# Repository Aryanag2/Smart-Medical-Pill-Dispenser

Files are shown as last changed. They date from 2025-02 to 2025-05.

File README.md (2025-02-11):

# Smart Medical Pill Dispenser (SMPD)

## Overview
The **Smart Medical Pill Dispenser (SMPD)** is an automated, cost-effective device designed to help users manage their medications efficiently. The system automatically sorts, stores, and dispenses pills at scheduled times while providing refill alerts and adherence notifications. The project is designed to minimize user dependency on manual sorting and reduce medication errors.

## Features
- **Automated Sorting & Dispensing**: Pills are sorted into dedicated compartments and dispensed at user-defined schedules.
- **Offline Operation**: Requires WiFi only for initial setup and updates; Bluetooth support enables configuration without constant internet access.
- **Refill & Adherence Alerts**: LED indicators and a web app notify users about missed doses and low stock.
- **Battery Backup**: Ensures continued operation during power outages.
- **User-Friendly Interface**: Web-based UI for configuration and monitoring.

## System Components
- **Microcontroller (ESP8266/ESP32)**: Handles scheduling, dispensing, and user notifications.
- **RTC Module**: Maintains accurate time, even during power failures.
- **Stepper Motors & Rotating Disk**: Facilitates pill sorting and controlled dispensing.
- **Weight Sensor (HX711 Load Cell)**: Tracks remaining pill stock and prevents over-dispensing.
- **3D Printed Enclosure**: Built with food-safe PLA/PETG for safe storage and dispensing.

## Repository Structure
```
📂 smart-pill-dispenser
├── 📂 firmware            # Embedded code for microcontroller
├── 📂 web-app             # Web-based UI for user interaction
├── 📂 hardware            # Circuit schematics, PCB designs, and 3D models
├── 📂 docs                # Design documents, proposal, and testing reports
├── 📂 notebooks           # Lab notebooks for individual team members
├── 📜 README.md           # Project overview and setup guide
├── 📜 LICENSE             # Open-source license details
```

## Setup Instructions
### **Hardware Setup**

### **Firmware Installation**

### **Web App Deployment**

## Testing & Validation

## Future Improvements

## License

## Contributors
- **Aditya Perswal** (apersw2)
- **Aryan Gosaliya** (aryanag2)
- **Aryan Moon** (aryanm7)

## Contact

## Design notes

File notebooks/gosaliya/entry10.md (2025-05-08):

### Entry 10: April 20, 2025

**Objectives:**
- Test breadboard setup in machine shop environment  
- Integrate enclosure with buttons and LEDs  
- Prototype 3D-printed trimmer parts to prevent pill jamming  

**Record (Right-Hand Page):**
- Brought breadboard prototype to machine shop for fit check in enclosure  
- Mounted LEDs for dose status and pushbuttons for pairing/refill alerts  
- Observed pill jams in rotating gate design; designed “trimmer” guides to smooth flow  
- Sent trimmer models to SCD for 3D printing in PETG to test clearances  
- Verified button actuation and LED visibility through enclosure cutouts  
- Created logo or ADAPT ( Adi/Aryan Dispenser Advanced Pill Technology) on CANVA

**Figures (Left-Hand Page):**
- `wooden-enclosure-with-logo-leds.png` — Photo of breadboard inside enclosure with buttons and LEDs installed and 3d printed trimmers installed  
- `logo.png` — logo for ADAPT

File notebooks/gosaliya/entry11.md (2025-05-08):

### Entry 11: April 27, 2025

**Objectives:**
- Validate full PCB functionality  
- Develop Electron desktop app for device control  
- Finalize firmware: HX711 calibration, BLE button link, flash-based schedule storage, and UI polish  

**Record (Right-Hand Page):**
- Received and tested revised PCB; all subsystems powered, no overheating  
- Calibrated HX711 in firmware for ±0.1 g accuracy; updated `readWeight()` routine  
- Mapped BLE “pair” button to trigger dispense and status commands  
- Implemented SPIFFS-based schedule storage in flash memory; supports up to 10 dose-times  
- Built Electron app with React UI: “Dispense Now,” “View Schedule,” and real-time status indicators  
- Iterated UI for user-friendly labels, feedback spinners, and error dialogs  

**Figures (Left-Hand Page):**
- `final-electron-demo.png` — Screenshot of Electron app dashboard  
- `working-pcb.png` — Photo of working PCB with LEDs and button mounted

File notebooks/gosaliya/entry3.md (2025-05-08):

### Entry 3: February 15, 2025

**Objectives:**
- Finalize mechanical enclosure design for machine shop  
- Design power-jack & backup battery circuit  
- Prototype enclosure & power circuit in KiCAD  

**Record (Right-Hand Page):**
- **KiCAD draft:**  
  - Created enclosure power-circuit schematic with DC jack, regulator footprints, and battery connector  
  - Labeled silkscreen for mounting holes and connector orientation  
  - Noted need for 12 V Li-ion rechargeable pack (≈2200 mAh)  
- **Battery backup:**  
  - Drew schematic for seamless switchover (diode-OR) between wall adapter and Li-ion pack  
  - Sized polyfuse and decoupling caps for 1 A peak load  
- **Component decision:**  
  - Switched from ATmega328 + HC-05 to ESP32-WROOM for built-in BLE, extra GPIO, and simplified PCB routing. No need for external RTC module

**Figures (Left-Hand Page):**
- `power.png` – power-circuit schematic  
- `battery_2way.png` – Battery-backup

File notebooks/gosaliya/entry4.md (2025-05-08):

### Entry 4: February 25, 2025

**Objectives:**
- Demonstrate breadboard prototype of interface, power, and mechanical subsystems  
- Validate core module integrations  
- Assess feasibility of rotating funnel design  

**Record (Right-Hand Page):**
- **Breadboard setup:**  
  - Used ESP32 dev kit (with onboard USB) for MCU and programming  
  - Connected DS3231 RTC module, HX711 + 1 kg load cell, standard servo, LEDs, and pushbutton  
- **Firmware validation:**  
  - Moved servo to 0 °, 90 °, and 180 ° positions reliably  
  - Verified load-cell reading lights LED when weight threshold exceeded  
  - Tested Bluetooth pairing via button and simple LED on/off commands  
- **Design evaluation:**  
  - Consulted machine shop: rotating funnel + stepper had clearance and alignment issues  
  - Decided to switch to a servo-driven shutter for dispensing  
- **Next steps:**    
  2. work with machine shop and breadboard-test the  design  
  3. Refine firmware timing and calibration for the new mechanism  

**Figures (Left-Hand Page):**
- `breadboard.png` — Photo of the breadboard prototype setup

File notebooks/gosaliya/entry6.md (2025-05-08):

### Entry 6: March 10, 2025

**Objectives:**
- Final team meeting before full breadboard demo  
- Refactor and modularize firmware functions  
- Calibrate sensors in code & verify accuracy  
- Note: web app functionality pending — focus remains on breadboard firmware  

**Record (Right-Hand Page):**
- **Modular code:**  
  - Split sketch into `dispensePill()`, `indexCompartment()`, `readWeight()`, `handleBTCommands()`  
- **Sensor calibration:**  
  - Tested with 1 g, 2 g, and 5 g weights; adjusted calibration factor for consistent ±0.2 g readings  
- **Persistence & scheduling stub:**  
  - Prepared SPIFFS routines using `Preferences` to store dose-times offline  
  - Added RTC-driven trigger logic; UI hookup deferred until web-app code is ready  
- **Failsafe & debugging:**  
  - Added error-LED blink on stall detection  
  - Serial logging timestamps each state and error for tuning timing constants
- Received mechanical enclosure from machine shop

**Figures (Left-Hand Page):**
- `basic-sketch.png`- Basic sketch showing servo control
- `wooden-enclosure.png` - Received mechanical enclosure from machine shop with servos, laod cell and pills

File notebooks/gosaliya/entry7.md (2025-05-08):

### Entry 7: March 17, 2025

**Objectives:**
- Conduct full breadboard integration demo  
- Validate end-to-end dispensing cycle  
- Identify firmware refinements before design review  

**Record (Right-Hand Page):**
- Assembled ESP32, , load-cell amplifier, servo motors, LEDs, button, and battery backup on the breadboard  
- Uploaded consolidated firmware with modular functions (`dispensePill()`, `indexCompartment()`, `readWeight()`, `handleBTCommands()`)  
- Ran demo sequence: wake, dispense dose, verify weight, signal success via LED  
- Measured average dispense latency: 1.8 s  
- Logged dispense errors for tuning threshold and timing constants  
- Team feedback: shutter mechanism consistent; LED alerts clear; adjust weight threshold by ±0.3 g  
- Prepared notes for upcoming design review and final paper  

**Figures (Left-Hand Page):**
- `breadboard.png` – Photo of integrated breadboard assembly  
- `basic-blueooth.png` - Basic bluetooth connectivity from ES32

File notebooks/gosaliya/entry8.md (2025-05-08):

### Entry 8: April 6, 2025

**Objectives:**
- Prototype web interface for device control & monitoring  
- Integrate JavaScript frontend with device via BLE/WebSocket  
- Test UI commands for dispensing and status updates  

**Record (Right-Hand Page):**
- Created basic web app structure in `index.html` with buttons for “Dispense Dose” and “Check Status”  
- Implemented BLE connection and command handlers in `main.js`  
- Developed `demo.js` to wire up UI buttons to BLE commands and display device responses  
- Verified browser↔device communication: “Dispense” and “Status” operations complete in 2–3 s  
- Noted occasional packet loss under weak signal; plan to add retry logic and visual feedback (spinner)  
- Defined next steps: full feature integration, robust error handling, and UI styling  

**Figures (Left-Hand Page):**
- `basic-webapp.png` — Screenshot of web app dashboard with control buttons

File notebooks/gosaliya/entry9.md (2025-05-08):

### Entry 9: April 13, 2025

**Objectives:**
- Test first full PCB revision (PCB1) with all subsystems  
- Diagnose power-subsystem failures (trace width, overheating)  
- Perform tolerance & thermal analysis  
- Design and order revised power-only PCB  

**Record (Right-Hand Page):**
- PCB1 arrived; soldered ESP32, hx711, servos, LEDs & button, and power regulators  
- Powered on: observed 5 V rail drop to 4.2 V under 500 mA load and regulator surface overheating after ~5 min  
- Measured PCB trace resistance; calculated I²R losses vs. expected voltage drop  
- Conducted tolerance analysis on regulator dropout voltage and copper trace ampacity  
- Determined that power traces (0.3 mm width) are undersized for peak currents  
- Decided to isolate power stage onto its own PCB with 1 mm-wide traces, added thermal vias and larger copper pours  
- Placed order for power-only PCB revision; delivery expected in 2 weeks  

**Figures (Left-Hand Page):**
- `final-pcb.png` - Kicad for PCB ordered

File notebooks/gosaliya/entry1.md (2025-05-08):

### Entry 1: January 25, 2025

**Objectives:**
- Summarize challenges in medication adherence for seniors  
- Review existing smart-dispensing solutions on the market  
- Define clear design goals (cost, accuracy, connectivity, power backup)  
- Sketch the initial system concept and high-level architecture  

**Record (Right-Hand Page):**
- **Demographics & adherence:**  
  - U.S. 65+ population grew by 9.4 % from 2020 to 2023  
  - 54 % of seniors take four or more prescription drugs  
  - 50 % of doses are forgotten or mistimed  
- **Financial impact:**  
  - Average annual medication spend ≈ \$800 per user  
  - Non-adherence wastes up to 50 % of that cost annually  
- **Competitive analysis:**  
  - **Hero dispenser:** \$540/year subscription; Wi-Fi only  
  - **MedMinder & Petal:** similar price points, require constant internet  
- **Identified user needs:**  
  - **Upfront cost ≤ \$250**; **server fees ≤ \$5/month**  
  - **Offline-first operation** after initial Bluetooth setup  
  - **Simple interface:** LEDs for dose & refill status; mobile web-app alerts  
  - **Battery backup** to cover power outages and maintain RTC  
- **Design targets:**  
  - **Dispensing accuracy ≥ 98.4 %** per scheduled dose  
  - **Alert latency < 5 seconds** from scheduled dispense time  
  - **Refill notification** when pill stock ≤ 10 %  
- **Next steps:**  
  1. Finalize and print high-level block diagram  
  2. Source candidate modules for each subsystem  
  3. Prepare parts list for initial breadboard prototyping  

**Figures:**
- `hero_device.jpeg` – Photo of the Hero smart dispenser (competitor device)  
- `hero_blockdiagram.png` – Hero’s high-level system block diagram

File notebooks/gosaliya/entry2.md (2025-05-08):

### Entry 2: February 8, 2025

**Objectives:**
- Decompose system into major subsystems  
- Survey existing modules & designs  
- Finalize top-level parts list  

**Record (Right-Hand Page):**
- **Six subsystems identified:**  
  1. Real-Time Clock + battery backup  
  2. MCU & comms (ESP8266 → ESP32)  
  3. Motor control (stepper & servo drivers)  
  4. Weight sensing (HX711 + load cell)  
  5. Mechanical housing & pill routing  
  6. User interface (LEDs, buzzer, button, web-app)  
- **Module survey notes:**  
  - RTC: DS3231 (±2 ppm accuracy, coin-cell backup)  
  - MCU: ESP8266 dev-kit prototyping → ESP32-WROOM for more I/O & BLE  
  - Drivers: L298N for stepper; HS-318 servo for funnel shutter  
  - Sensor: 1 kg load cell + HX711 amplifier (±0.2 g)  
  - Enclosure: PLA 3D-print core, wood frame from machine shop  
- **Integration sketch:**  
  - Data-flow arrows between MCU, sensors, actuators, and UI drawn for clarity  
- **Final parts list:**  
  - ESP32-WROOM-32D  
  - DS3231 RTC module  
  - HX711 + 1 kg load cell  
  - L298N motor driver board  
  - HS-318 servos × 2  
  - LEDs: power, mode, refill, and 3× compartment indicators  
  - Pushbutton (pairing/reset)  
  - Regulators: 12 V→5 V (LM7805), 5 V→3.3 V (LP2950)  
  - 12 V Li-ion backup pack  

**Figures (Left-Hand Page):**
- `esp32.jpeg` – ESP32-WROOM-32D module photo  
- `ds3231.jpeg` – DS3231 RTC module photo

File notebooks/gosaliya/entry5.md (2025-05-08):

### Entry 5: March 3, 2025

**Objectives:**
- Kick off firmware development on the breadboard  
- Validate control of mechanical & sensing subsystems  
- Lay groundwork for mobile/web interface commands  

**Record (Right-Hand Page):**
- **Arduino IDE setup:**  
  - Installed ESP32 core, HX711 and Servo libraries  
  - Created sketch with `setup()` and `loop()` stubs  
- **Breadboard firmware tests:**  
  - Servo on pin 4 moved to 0°, 90°, and 180° reliably  
  - Stepper via L298N indexed compartments; tuned `stepDelay` to correct step errors  
  - Load cell calibrated using `scale.set_scale()` and `scale.tare()`, LED on pin 12 lights when weight threshold exceeded  
- **Bluetooth pairing & UI stub:**  
  - Button on pin 5 initiates pairing mode via BLE  
  - Sketch logs “LED ON”/“LED OFF” commands over Serial; full web-app integration to come  
- **Code structure:**  
  - Implemented basic state machine (`IDLE`, `PAIRING`, `DISPENSE`, `ERROR`) for early prototyping  

**Figures (Left-Hand Page):**
- `code_flow.png` – Firmware Code Flow Diagram  
- `data_flow.png` – Data Flow Diagram

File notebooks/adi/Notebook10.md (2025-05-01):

# Notebook 10

**Date:** April 20th, 2025

## Objectives
1. Power the Breadboard with the Power Only PCB
2. Create a Last Chance PCB with through holes only
3. Switch to programming with a breakout board
4. Implement 3D prints for compartment trimmers

## Record of Work

Created the "Last Chance" PCB and ordered it. Hopefully it comes in on time, this is our 6th and final PCB order likely. Used through holes only so when it does come we can solder it very quickly.

Need to buy solder paste still for the ESP32-WROOM-32D. I don't remember if I wrote in why we switched to 32D from 32U but it was because it had an antenna and only costed a few more cents.

### Last Chance Schematic View
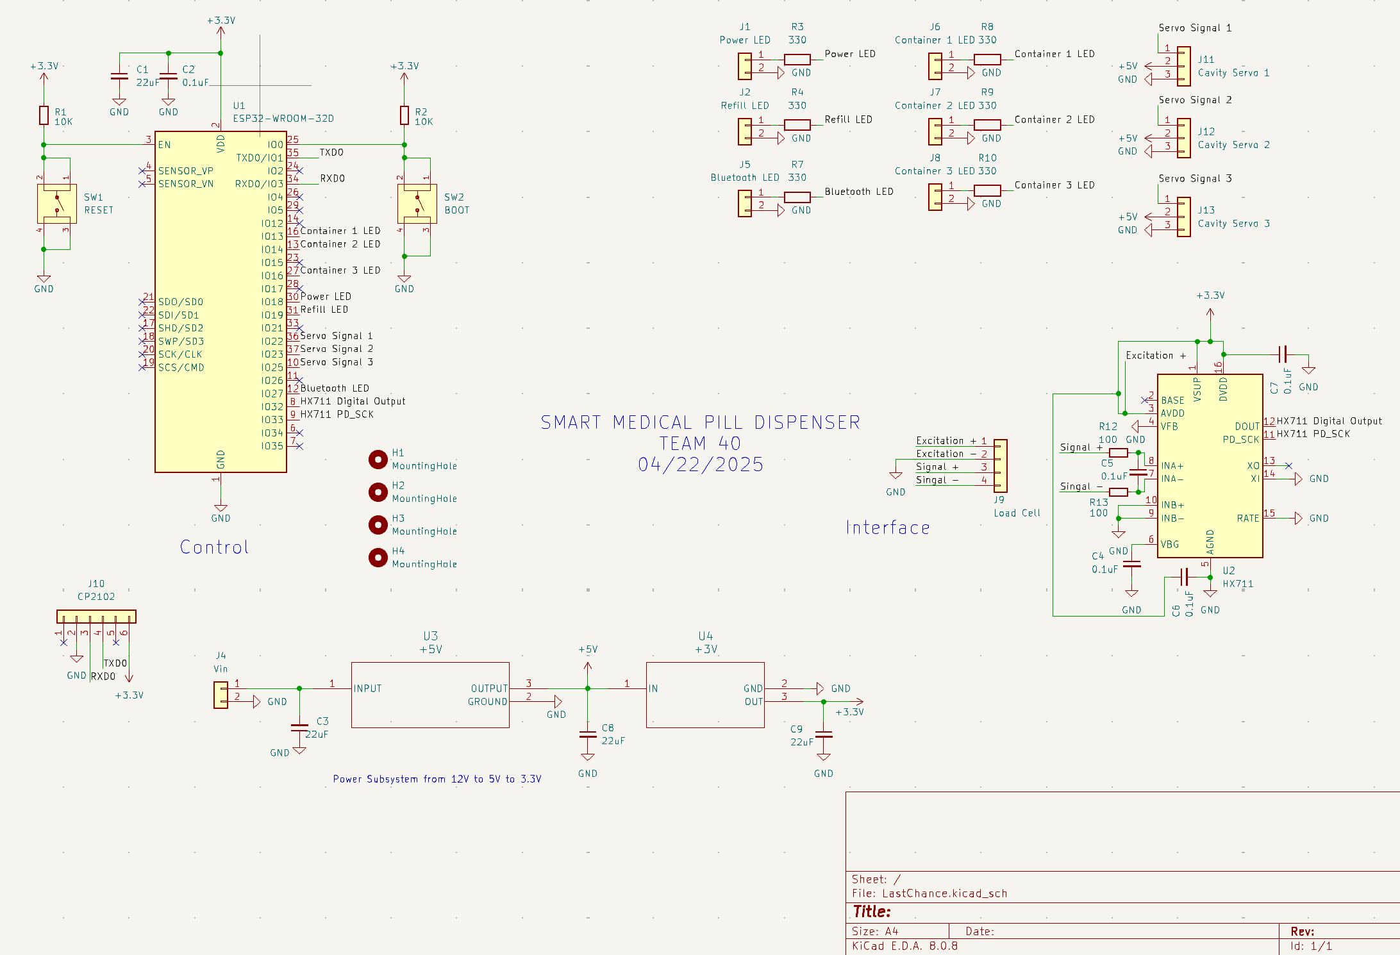
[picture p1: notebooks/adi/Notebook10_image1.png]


### Last Chance PCB View
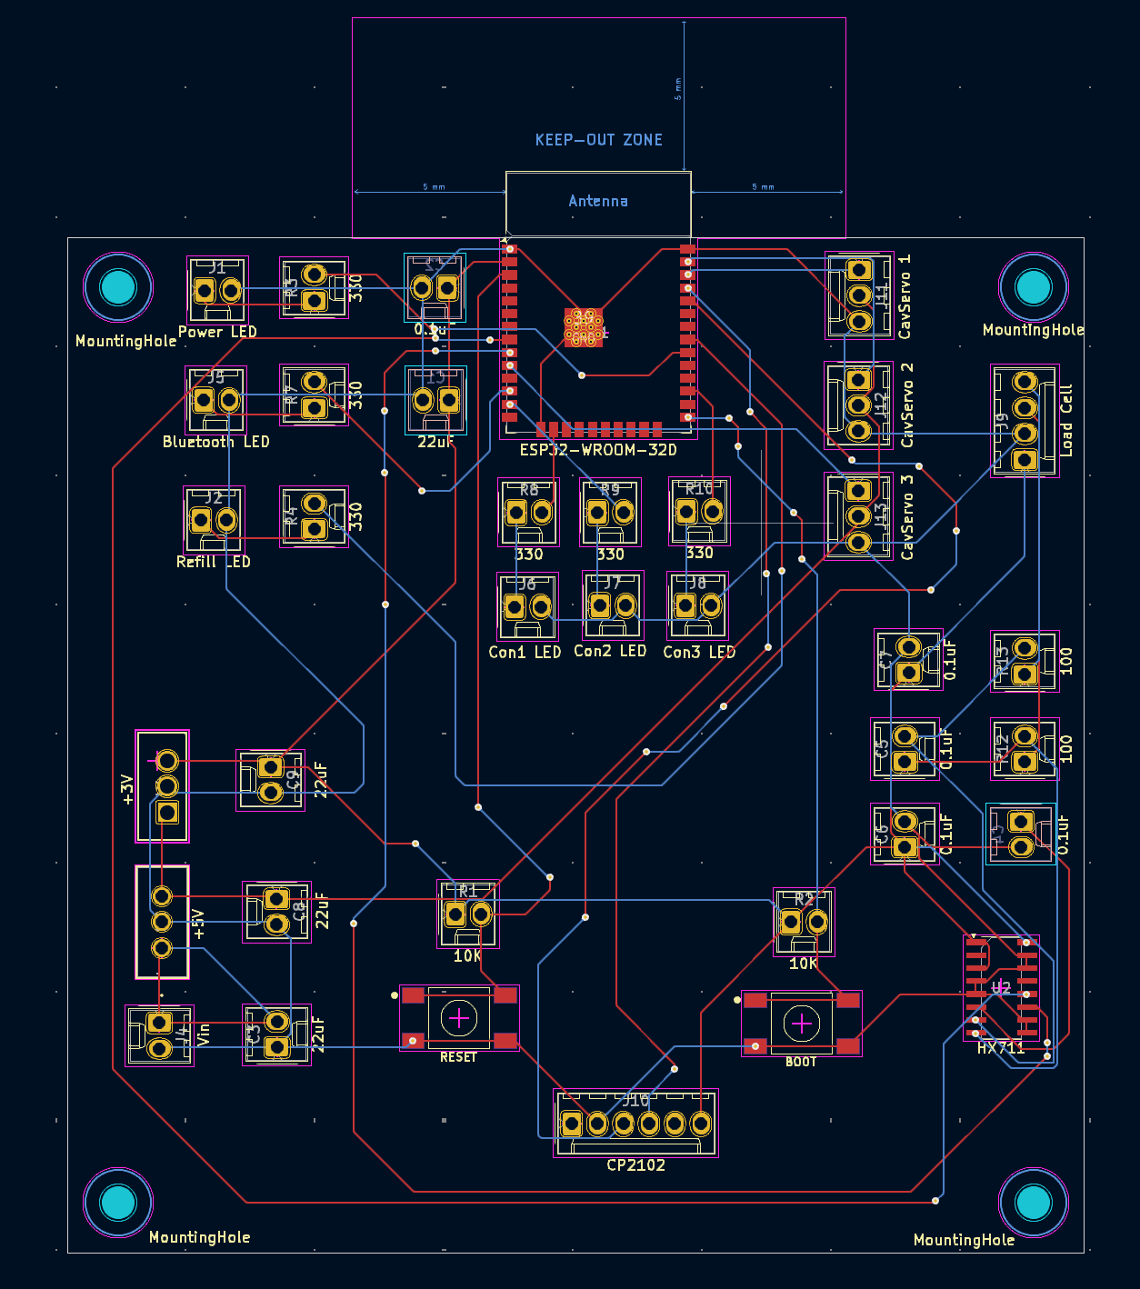
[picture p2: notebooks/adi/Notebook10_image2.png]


The arduino code is having some issues with dispensing on time when the scheduled medications pop up. The microcontroller can take commands pretty quickly but it does them one at a time. Maybe it is having issues because we are sending so many commands at once. Right now we have about 1,400 lines of code in our Arduino IDE, I think I can drop that to 900 though and clean up / refactor the code a ton.

### Arduino Code
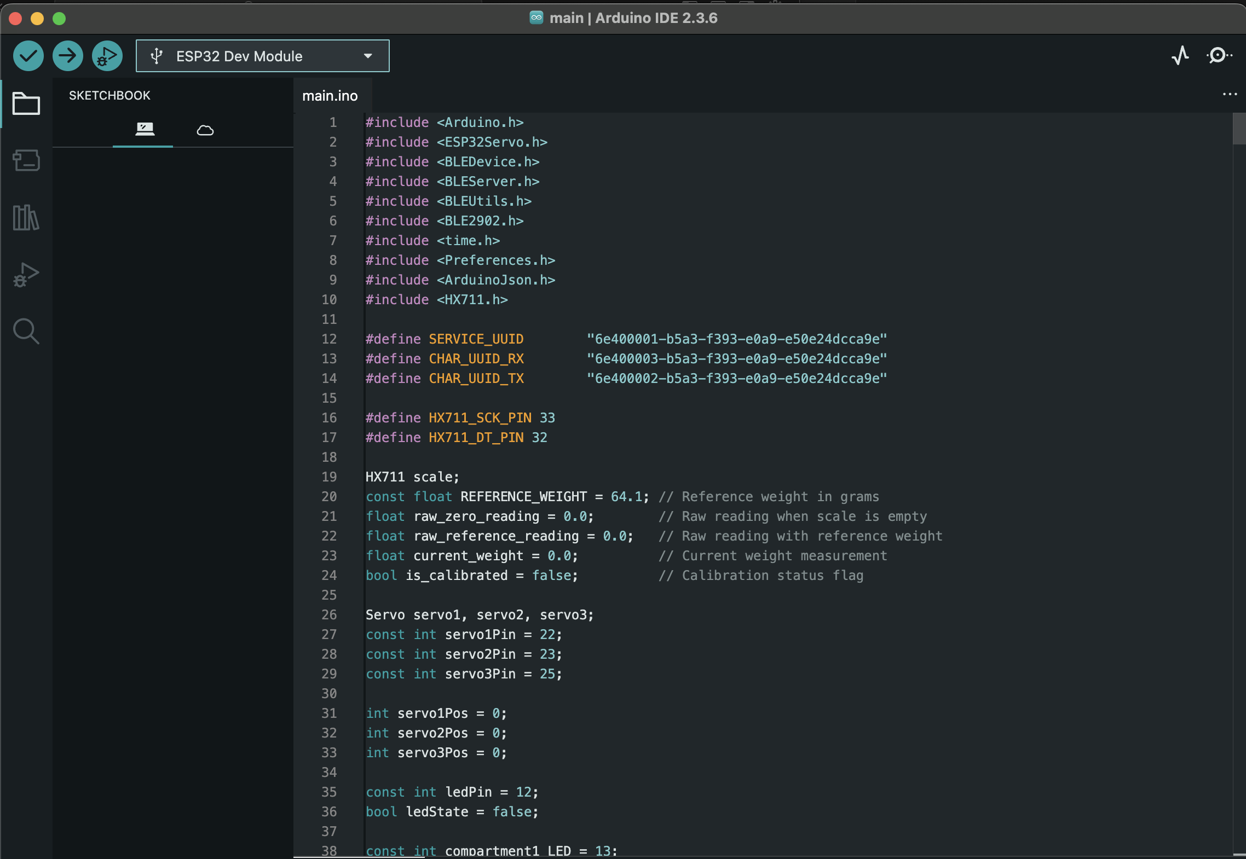
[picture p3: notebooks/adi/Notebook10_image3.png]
Arduino Code


The USB-UART breakout board should help a ton. We broke so many Micro USB ports because of poor soldering or didn't have the FT232RL soldered properly.

### CP2102 Breakout Board
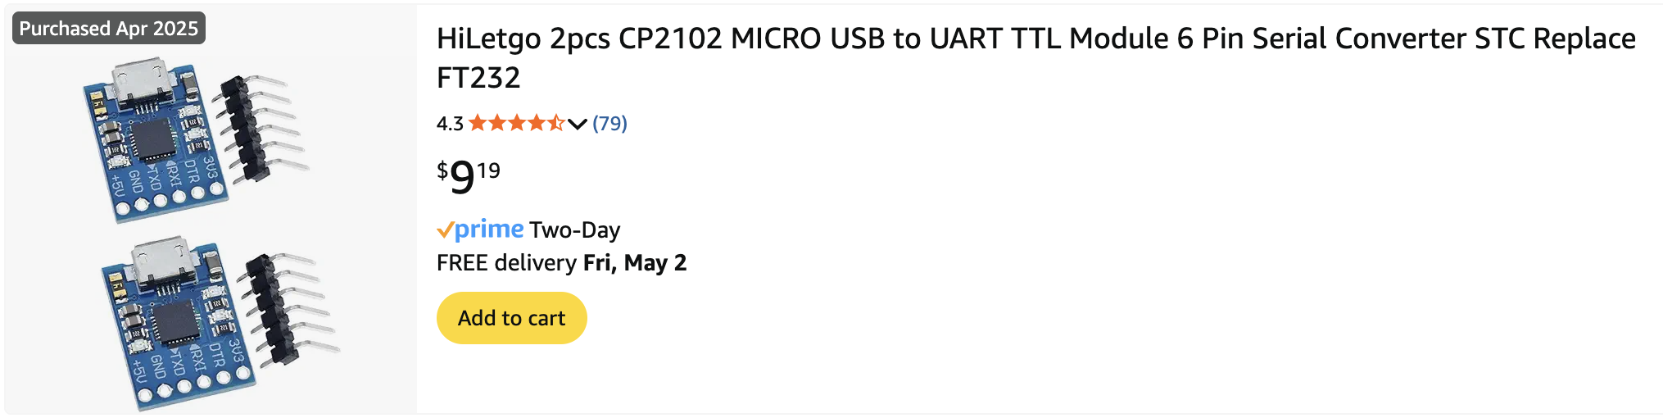
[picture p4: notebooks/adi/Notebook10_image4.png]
CP2102 Breakout Board


Learned AutoCAD for this class. This trimmers should come in soon, will go to SCD and have them printed out. They said it should only cost about $1.80.

### 3D Prints
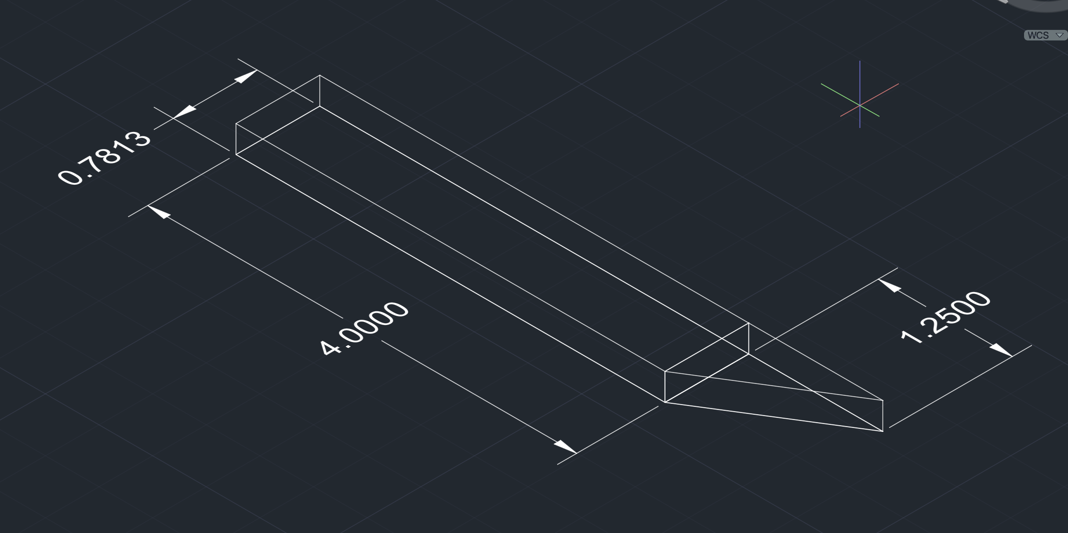
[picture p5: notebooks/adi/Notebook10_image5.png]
Compartment 1

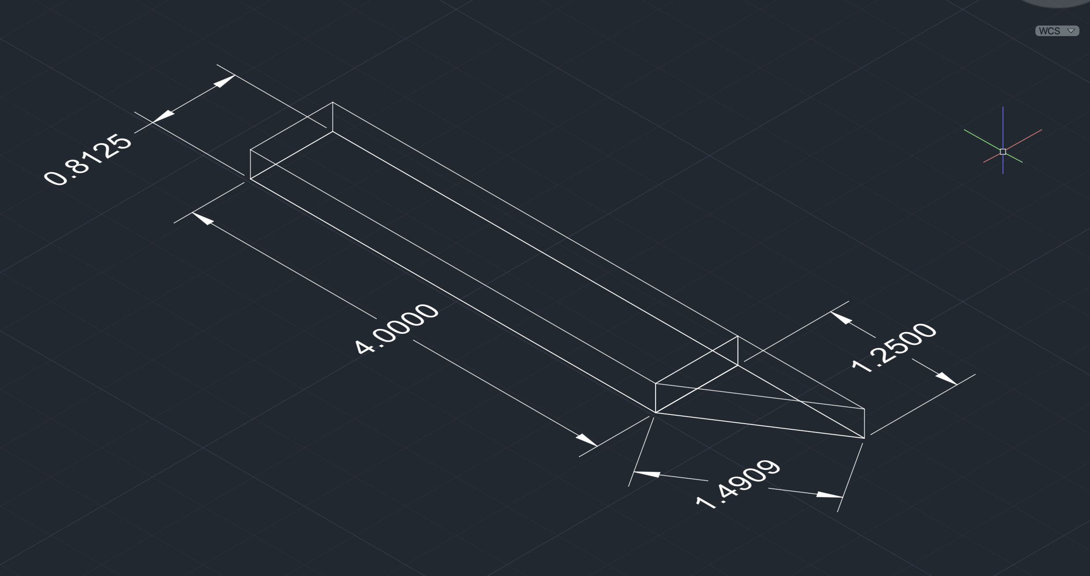
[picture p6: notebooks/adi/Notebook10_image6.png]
Compartment 2

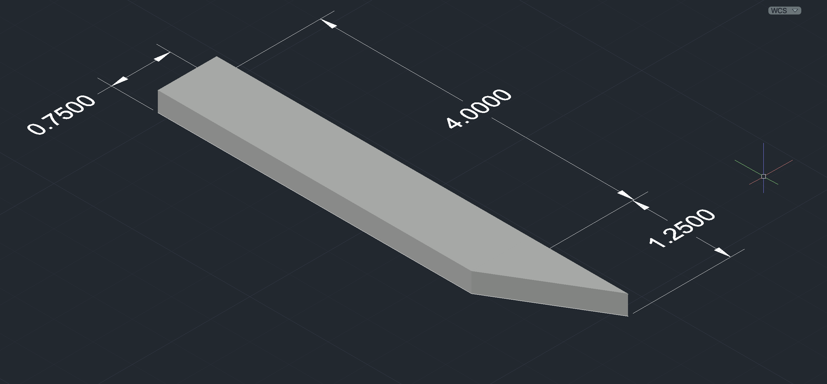
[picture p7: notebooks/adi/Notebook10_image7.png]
Compartment 3


## Personal Thoughts
The power only PCB is working correctly outputting around 5.07V and 3.301V respectively. Tried to put power in directly to the output pins of the regulator through holes of the original PCB but that ended up leading to 1.7V for the 5V through hole or 0.6V for the 3.3V through hole. Going to need to figure out a way to power the final design with this PCB. That seems to be having the power subsystem on the PCB and the rest outside it. Hopefully we get a good set of points from the final demo rubric, and the final last chance PCB can come in time.

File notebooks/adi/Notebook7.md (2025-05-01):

# Notebook 7

**Date:** March 29th, 2025

## Objectives
1. Complete PCB for CP2102 for Order 3
2. Complete PCB for FT232RL for Order 4
3. Order Extra Parts

## Record of Work
1. 2N2222A - Transistor - Self Help Drawers
2. MBR1100 - Schottky Diode - Self Help Drawers
3. CP2102 - Ordered 5
4. ESP32-WROOM-32D - Ordered 10
5. ESP32-WROOM-32U - Ordered 5

Working with both USB-UART bridges since one is in the self help drawers and the other we bought in bulk. We can try to make the FT232RL work and by the time the CP2102 comes we can switch over to it if necessary. From what I have read online though, the FT232RL should work just fine.

### Schematic
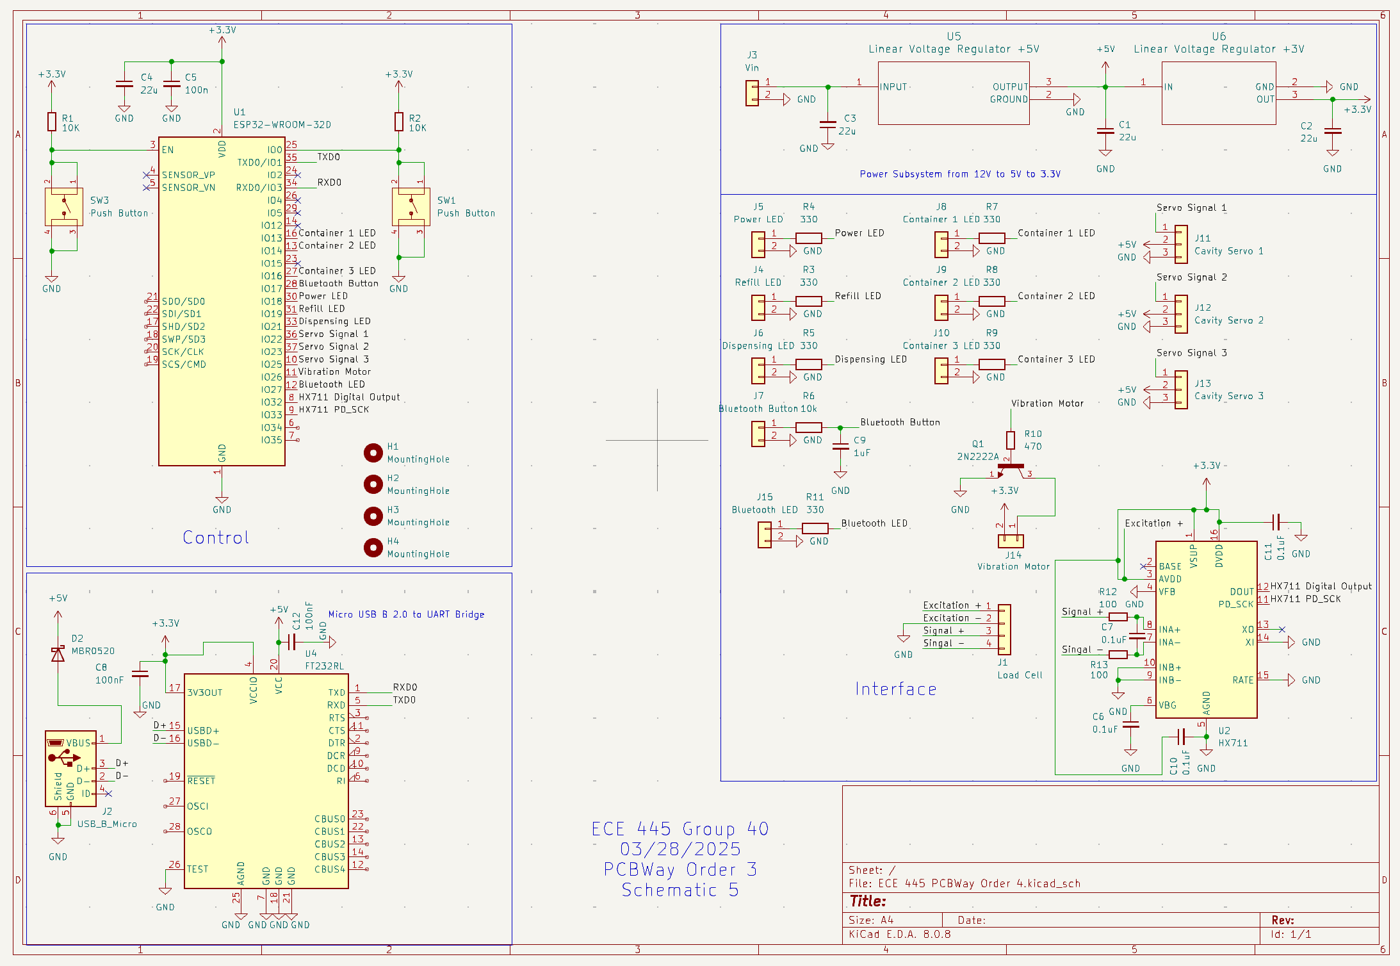
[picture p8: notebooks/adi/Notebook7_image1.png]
Schematic View 1

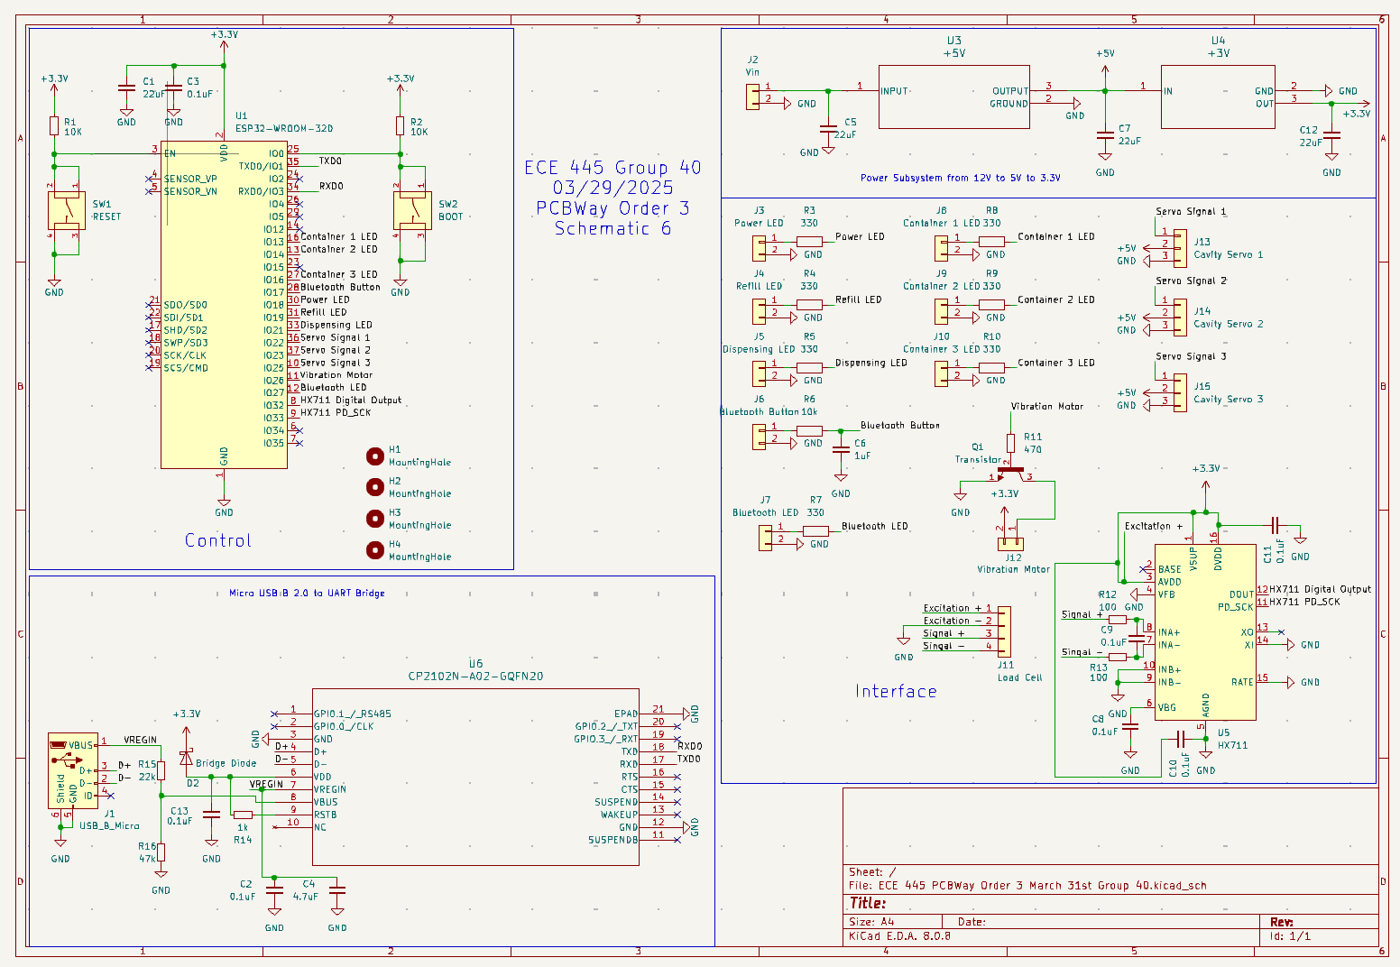
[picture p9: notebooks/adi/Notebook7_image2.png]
Schematic View 2


### PCB
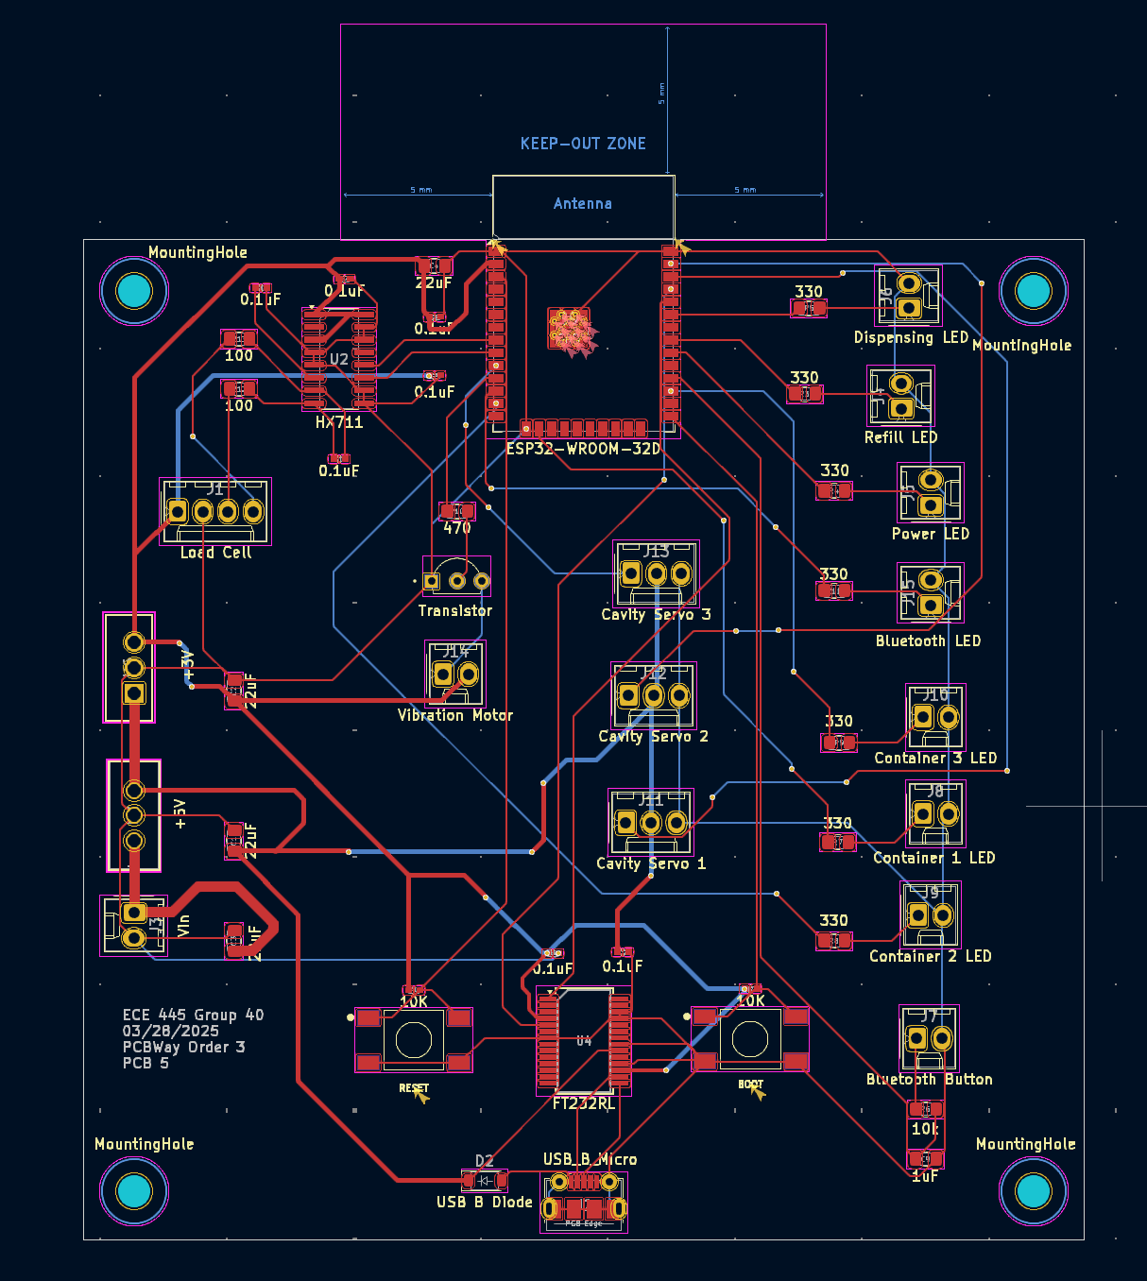
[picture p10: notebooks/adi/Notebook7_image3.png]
PCB1 View

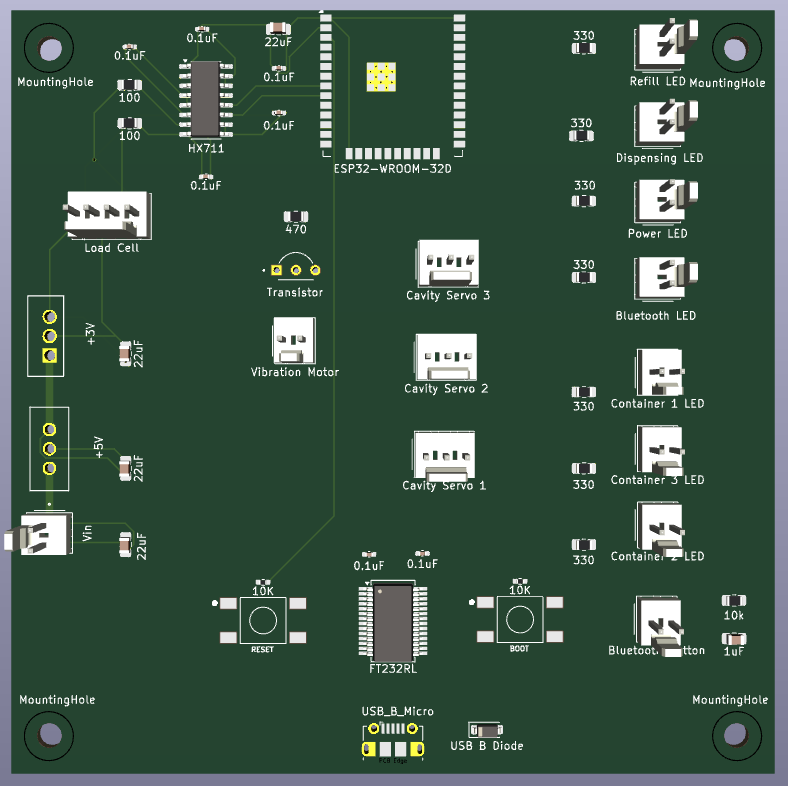
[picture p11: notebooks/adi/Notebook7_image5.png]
PCB1 3D Design


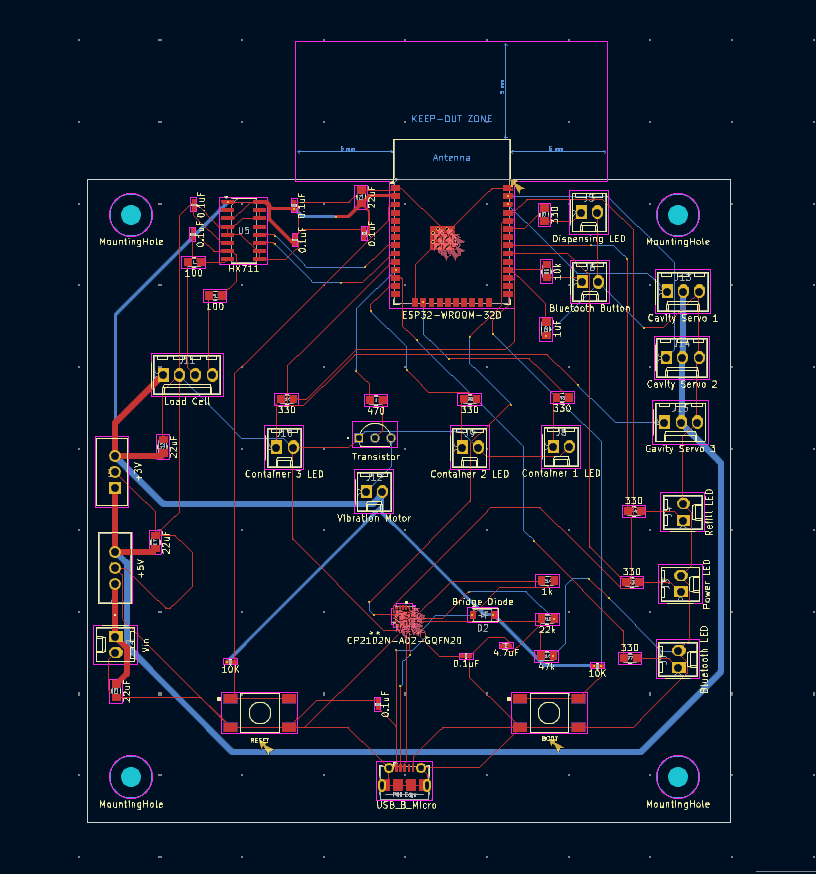
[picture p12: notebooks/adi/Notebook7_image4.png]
PCB2 View

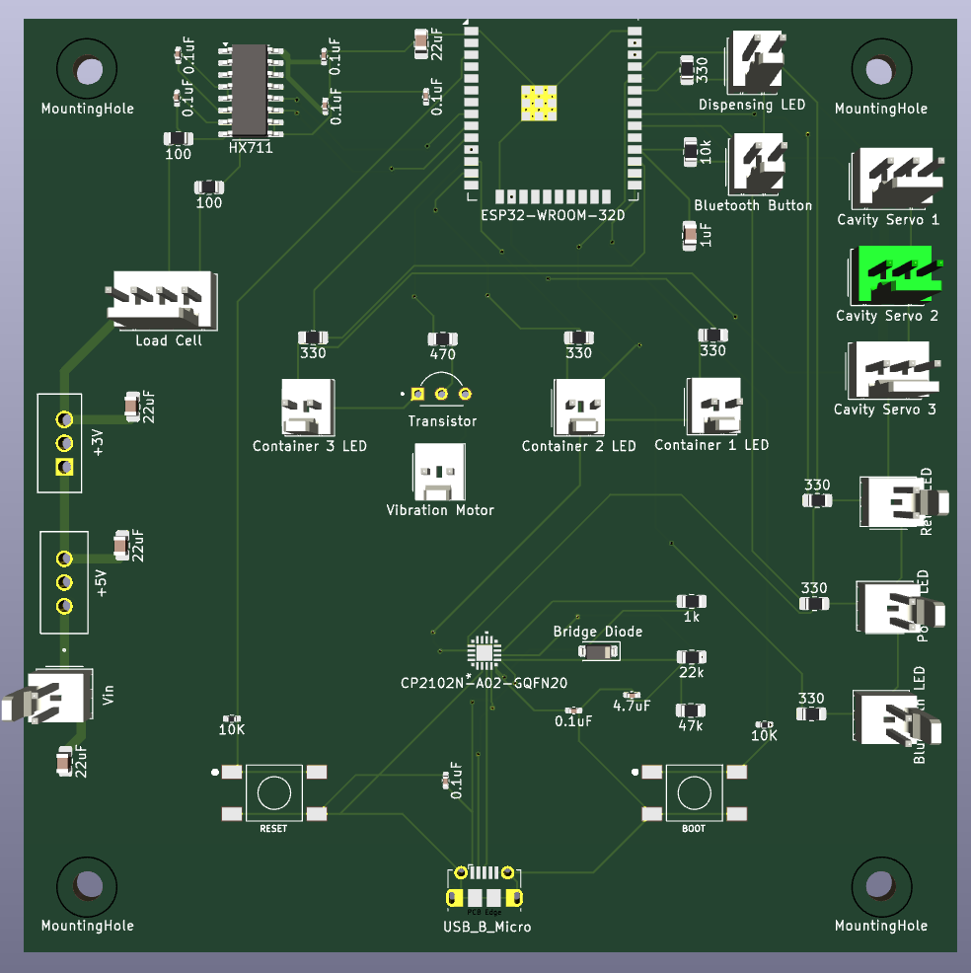
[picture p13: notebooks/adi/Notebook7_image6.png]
PCB2 3D Design


## Personal Thoughts
Switched to a USB to UART bridge that we can get from self help drawers and easier to solder. Worried about finishing PCB on time, mainly due to delivery delays. Just ordered another round of PCBs on our own dime as well. Wiring and schematics make sense, so atleast we are going faster in that regard now.

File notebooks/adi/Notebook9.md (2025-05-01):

# Notebook 9

**Date:** April 13th, 2025

## Objectives
1. Get the Electron App to work
2. Get the Power Subsystem to work
3. Get new parts from the self help drawer
4. Figure out how to solder the diode since we dont have surface mounts
5. Figure out how to get the long pills to not jam or clog the cavity

## Record of Work

The 5V regulators are overheating so we switched to the L7805CV 5V Linear Regulator since it can handle up to 35V and can be attached to a heat sink.

The 3.3V Regulators don't seem to be working any longer, even on the breadboard. So we are going to try out the LP2950CZ. We don't know why none of the 3.3V linear regulators are working.

The Power Subsystem on the PCB when tested taking in 5V and 3.3V into what would be the output pins of the linear regulators, showed that the 5V dropped to 1.7V or the 3.3V dropped to 2V when both pins were having power sent in.

Our PCB's overheating because the trace widths are too large, most likely.

We are going to pull our power subsystem out into a seperate PCB to have it work

We ran out of FT232RL chips in the self help drawers, and don't have time to order more so we are switching back to CP2102 but its going to be hard to solder these on.

### Electron App
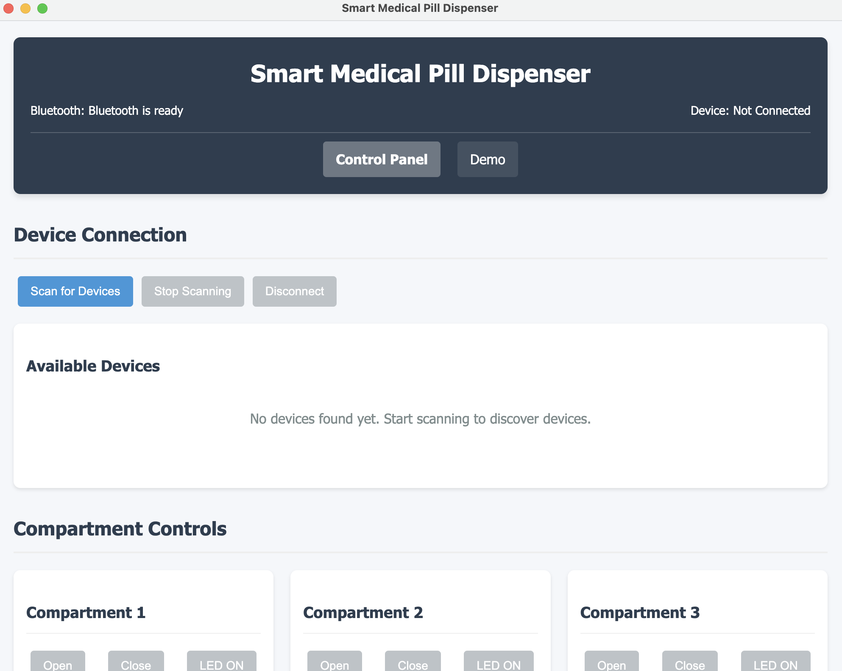
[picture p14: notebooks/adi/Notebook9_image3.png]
App View


We added some neat things like LED animations, persistence of schedule in the ESP32 using bits for keeping schedule.
Pack schedule data into a 32-bit integer:
- Bits 0-5: ID (0-63)
- Bits 6-10: Hour (0-23)
- Bits 11-16: Minute (0-59)
- Bits 17-23: Days of week (bit field)
- Bit 24: Active flag

Going to solder the Power only PCB without surface mounts, with through hole instead.

### Power Only Schematic
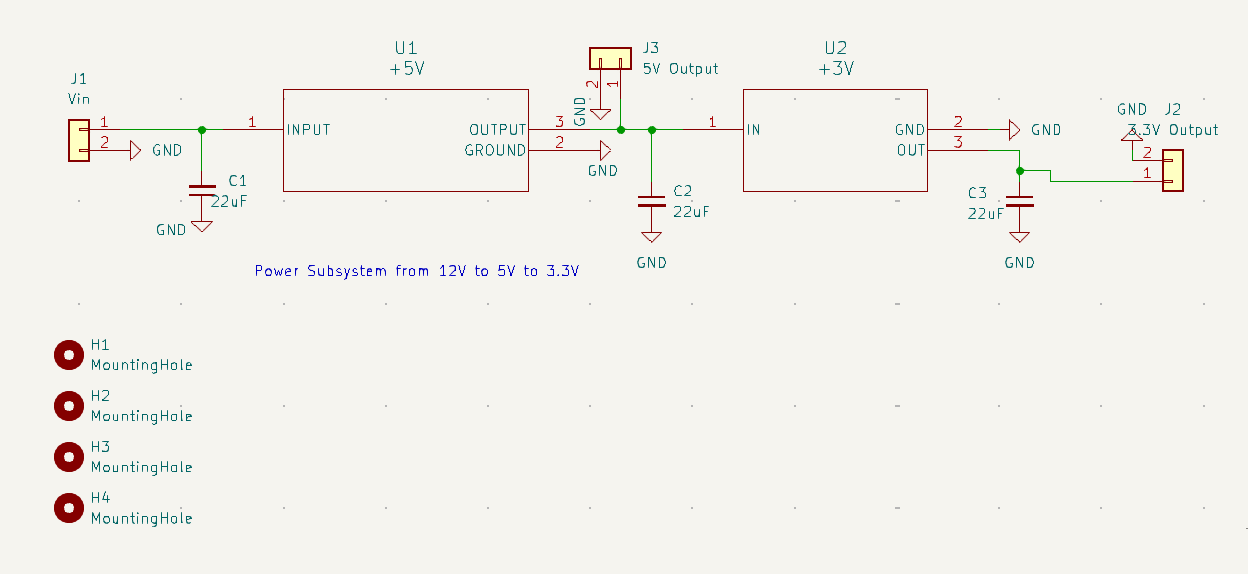
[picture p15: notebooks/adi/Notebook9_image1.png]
Schematic View


### Power Only PCB
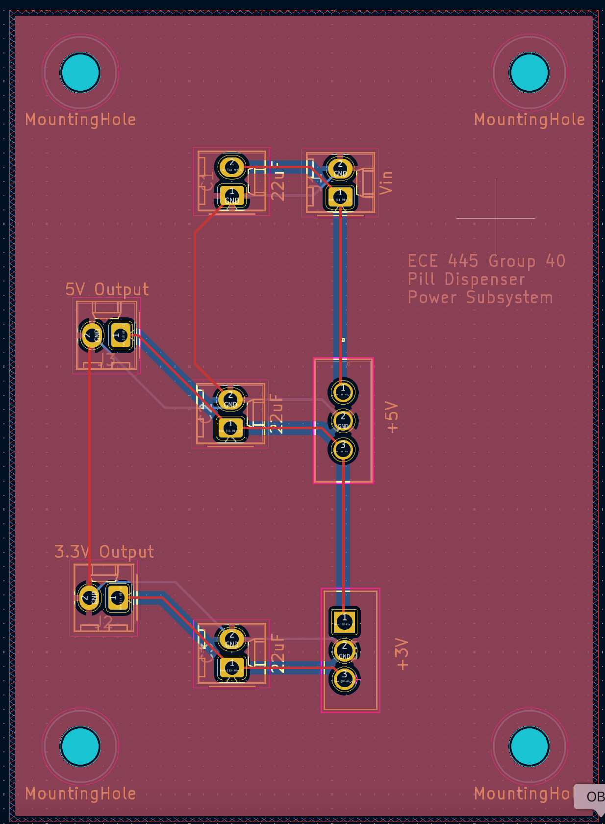
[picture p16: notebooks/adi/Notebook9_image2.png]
PCB View


We tried soldering the diode but it keeps breaking, I wonder if we really need it for the time being, or if we can do without.

## Personal Thoughts

Having to make A LOT of changes, kind of unsettling. We will likely need to use the dev board for the final demo. We do know what we would do to fix the PCB though, so hopefully that counts for something. Definitely learned a lot about engineering set backs and unaccounted for errors that can arise. For the pills that are jamming we are going to decrease the size of the container, so that they can hold less but jam less too.

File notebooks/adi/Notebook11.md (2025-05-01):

# Notebook 11

**Date:** April 27th, 2025

## Objectives
1. Solder the Last Chance PCB
2. Switch 100g sensor to 1kg sensor
3. Calibrate the 1kg sensor
4. Deploy app to App Store

## Record of Work

### Last Chance PCB Results
WE GOT THE PCB TO WORK. We were able to program a simple program making the light blink for bluetooth and the power light stay on the whole time. 

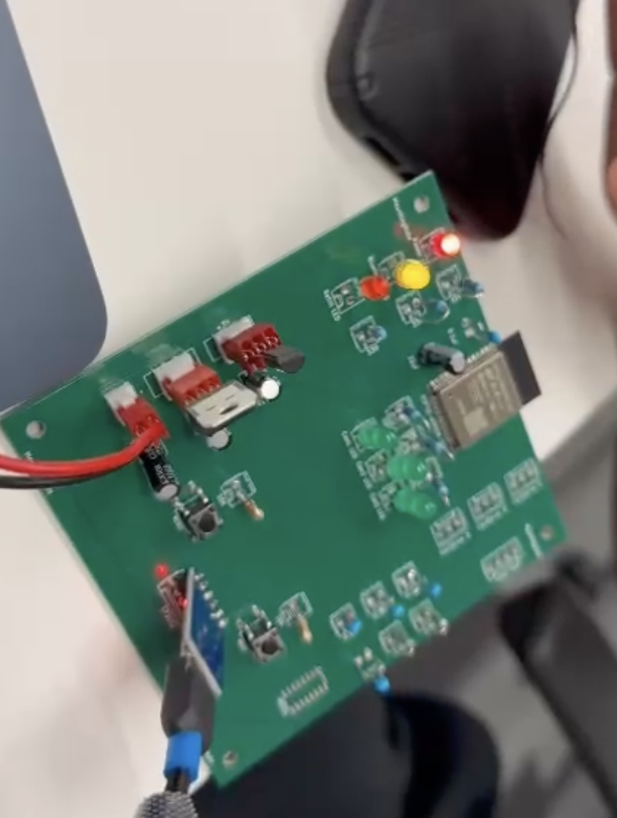
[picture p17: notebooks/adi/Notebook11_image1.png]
Soldered PCB View


CP2102 breakout board was soldered weirdly so its throwing some errors if its not placed properly, but that's fine, all that matters is that it works.

Had to stay with the dev board for the final demo though because we ran out of HX711 ICs, going to buy more and see if we can still have this working by the end,

### Switching from 100g Load sensor to 1kg
Going to ask Gregg to let us swap the load sensor as soon as possible. Tried to do it myself but the screws aren't long enough to reuse the 100g's on the 1kg's. 

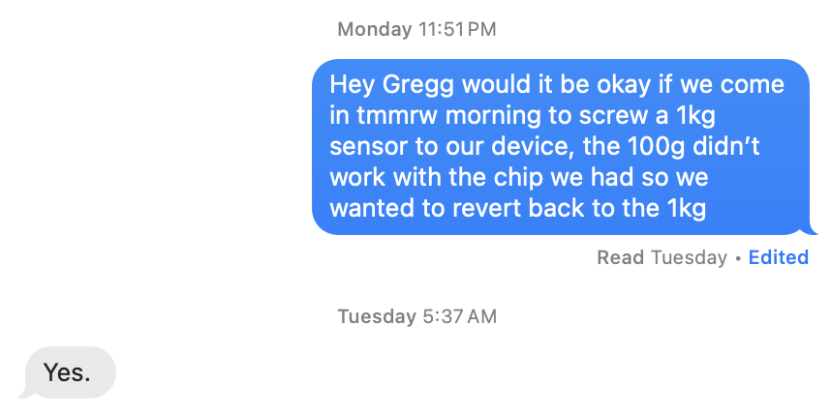
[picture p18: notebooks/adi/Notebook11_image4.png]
Machine Shop Texts to Swap Load Sensors


Had to swap the 100g for the 1kg because the HX711 can't reliably read the data from the 100g even with 80ms readings. It needs to use something like the AD7794 as an amplifier.

### Calibrating the 1kg load sensor
Calibrating the 1kg load sensor is taking a bit of time. We soldered it properly and the HX711 works well with it.
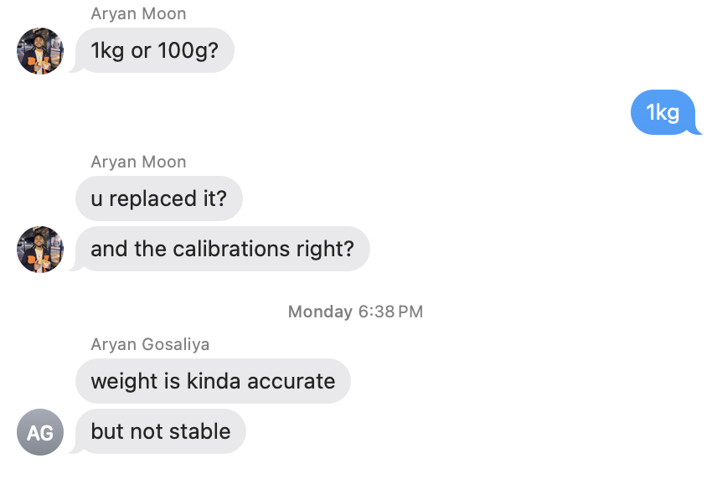
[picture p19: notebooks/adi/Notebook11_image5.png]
Group 40 Texts for Calibrating Load Sensor


Was able to calibrate it with the Airpods Pro Gen 2 which weight 61.4g. It's reliably reading 61.2g over and over again.
Group 40 Texts for Finishing Calibrating Load Sensor

### Deploying app to app store

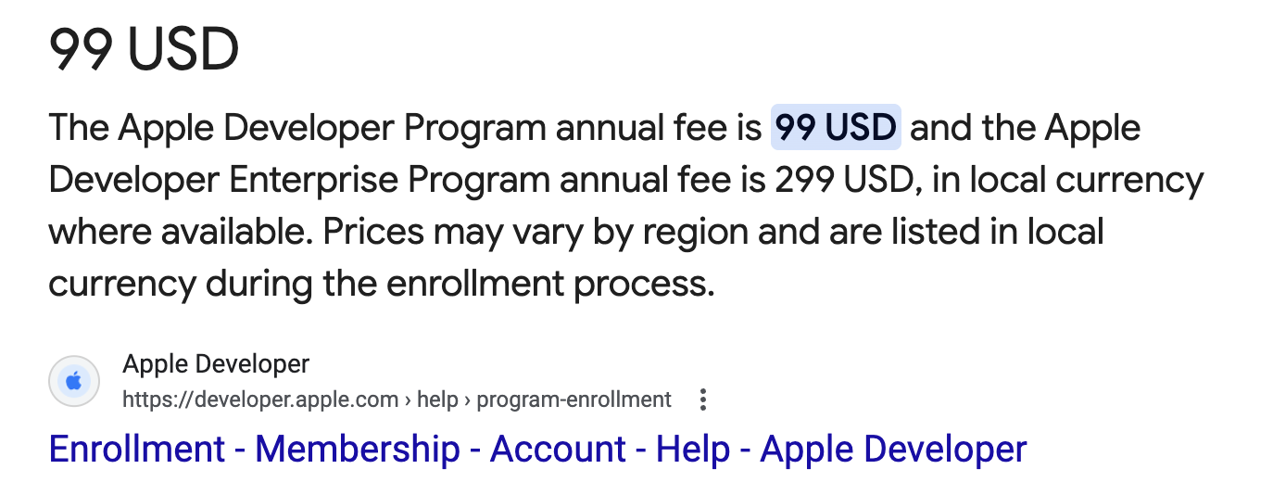
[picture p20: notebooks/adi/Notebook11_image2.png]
Cost of Apple Developer Program


Electron app is done but can't be deployed to app store because we aren't part of the apple developer program. Need to wait a few days and pay $99 so probably won't sign up for it. But, we do know it works.

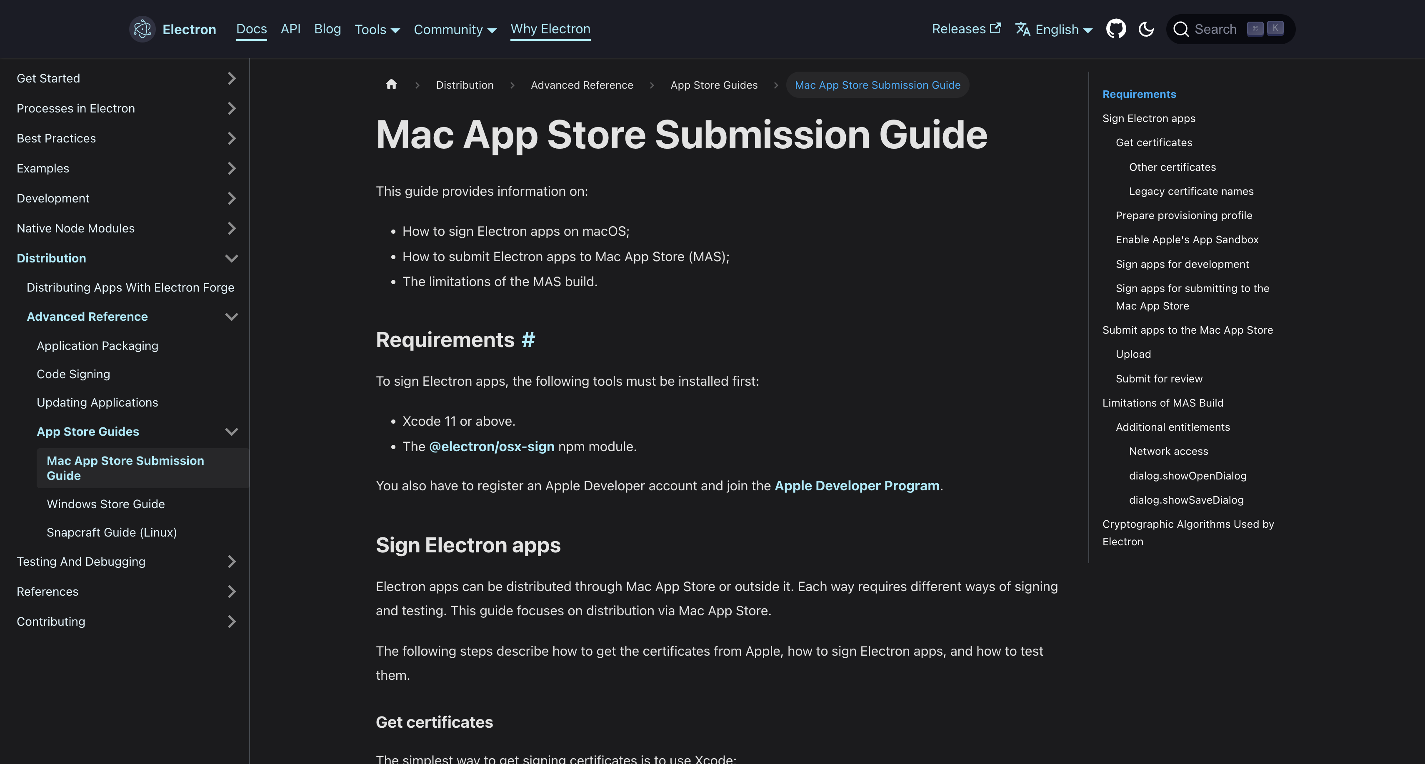
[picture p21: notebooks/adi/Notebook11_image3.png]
Electron to IOS App Store Deployment


## Personal Thoughts
Having to make A LOT of changes, kind of unsettling. We will likely need to use the dev board for the final demo. We do know what we would do to fix the PCB though, so hopefully that counts for something. Definitely learned a lot about engineering set backs and unaccounted for errors that can arise.

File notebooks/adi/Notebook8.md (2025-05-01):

# Notebook 8

**Date:** April 6th, 2025

## Objectives
1. Complete PCB for FT232RL for ECE Order 4
2. Solder PCB3-Personal using Stencil

## Record of Work

Not a huge update this week. We have been soldering all our PCBs mostly this week but realized that we should probably fix some of the accidental 90 degree angles we created. Probably will run into issues and need to order another PCB though since we are behind in testing by a good margin.

### Schematic
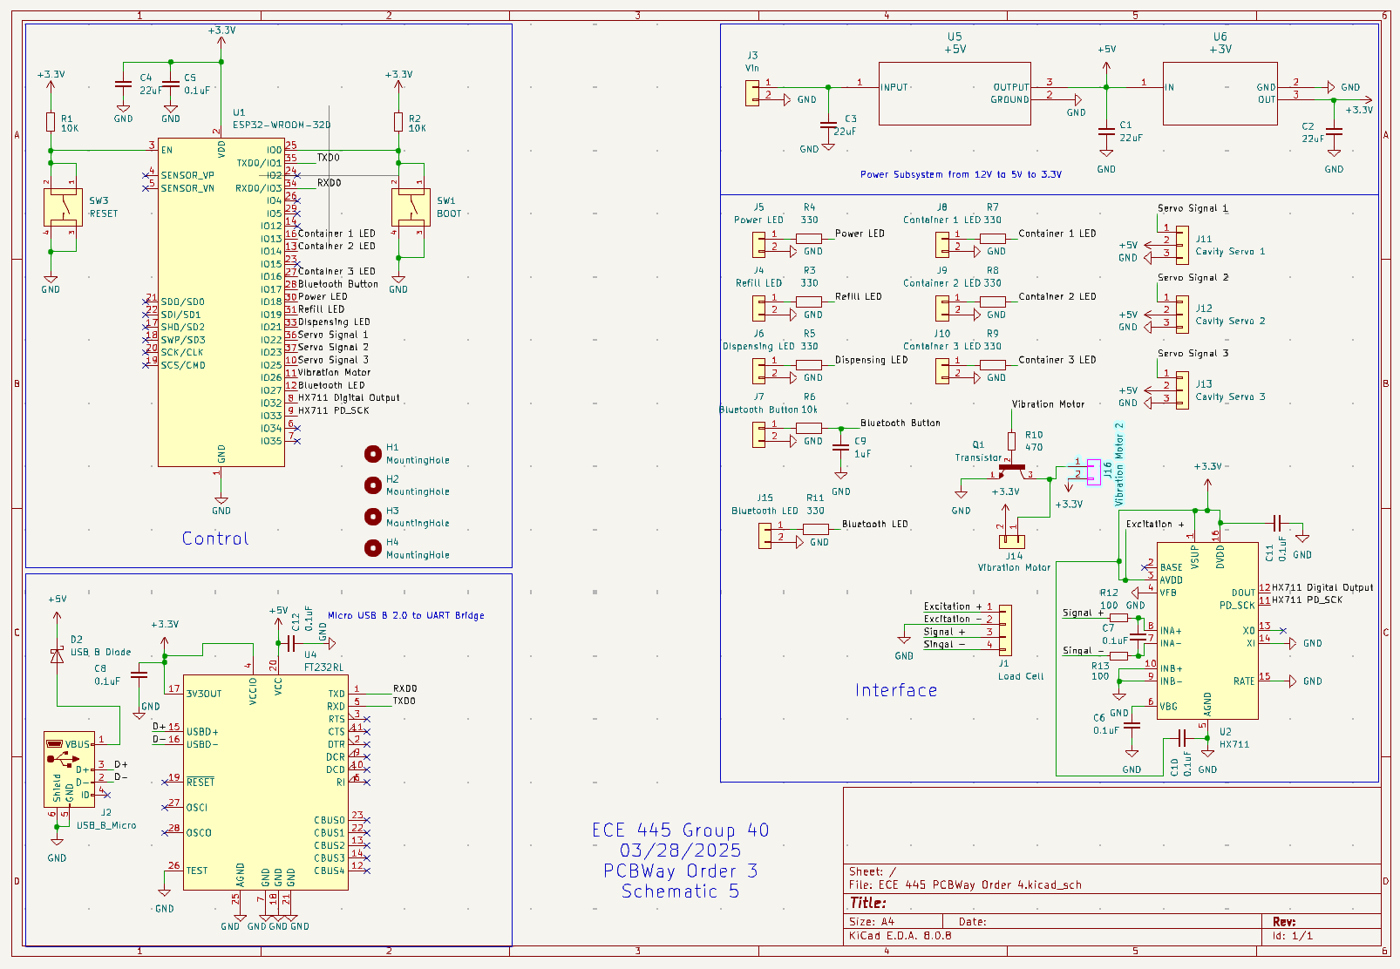
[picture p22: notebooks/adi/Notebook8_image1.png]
Schematic View


Found the stencil so we can start using soldering paste. I also need to start using flux more often as it is a good way to keep the soldering clean.

### PCB
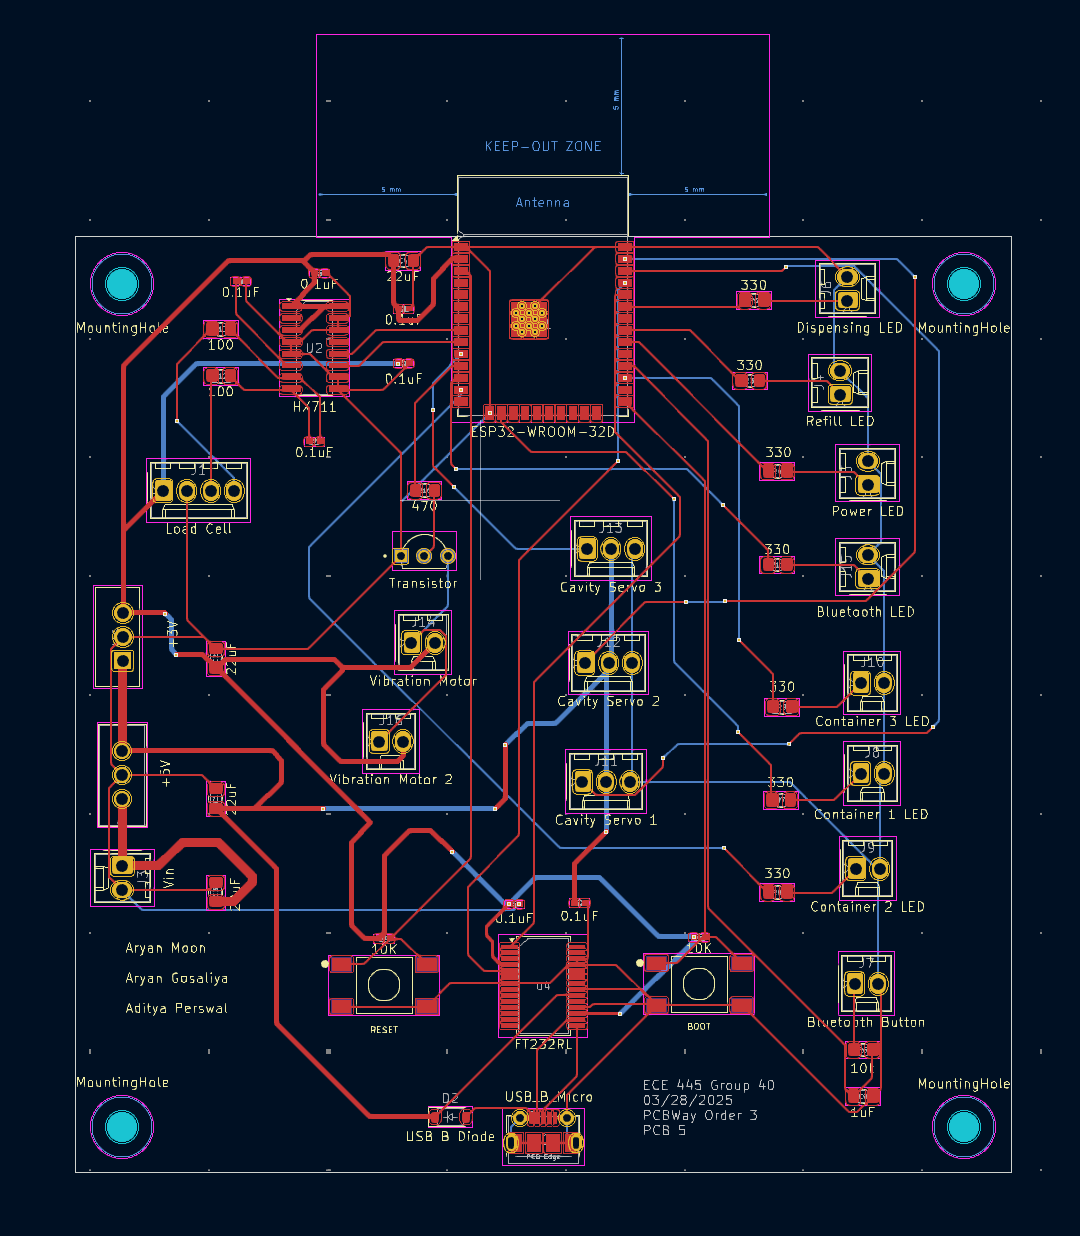
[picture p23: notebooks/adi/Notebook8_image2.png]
PCB View


## Personal Thoughts
Soldering with stencil is A LOT EASIER. PCB-Personal being soldered this week, but exams are slowing us down. Programming the web app too, Aryan Gosaliya just made the finalized logic map. On track, looking like no longer ahead of schedule though.

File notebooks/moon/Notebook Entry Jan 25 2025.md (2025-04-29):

# **Senior Design – Brain-storming Meeting Notes**

**Date:** January 25, 2025  
 **Location:** Suites at Third

---

## **Attendees**

* Aryan Moon

* Adi Perswal

* Aryan Gosaliya

---

## **Agenda**

1. Review broad problem areas of interest

2. Generate and rank project concepts

3. Identify top contenders for deeper research

4. Assign preliminary next-step tasks

| Idea | Problem Addressed | Key Features of the Project | Drawbacks |
| :---- | :---- | :---- | :---- |
| Smart Medical Pill Dispenser | Medication non-adherence in outpatient care | \- RFID-tagged bins for dose verification \- BLE to sync with phone / caregiver dashboard \- Weight sensor \+ HX711 for fill-level |  \- FDA / IEC-60601 compliance scope?  \- Battery life vs. Wi-Fi? |
| Smart Massage Sleeve for Athletes | Localized muscle fatigue & minor strains | \- IR thermography patch to find “hot spots” \- Pneumatic or vibro-motor arrays for massage \- Companion app tracks recovery heat maps |  \- Real-time thermal processing on-edge?  \- Sleeve bulk & user comfort during play |
| Assistive Object-Detection Glasses | Orientation cues for partially blind users | \- Stereo camera → onboard ML detection \- Bone-conduction audio for object call-outs \- Micro-LED spot in lens indicates sound origin |  \- Displaying light without glare / distraction  \- Latency of vision → audio → haptic loop |

*Smart Medical Pill Dispenser* edged out as the current front-runner, but we’ll keep all three alive until after discussing this with the TA and posting these on the web board as projects

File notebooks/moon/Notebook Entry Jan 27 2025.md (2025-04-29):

# **Personal Research Notebook – Concept Deep Dive**

*Aryan Moon* • January 27, 2025

---

## **1 ⎯ Smart Medical Pill Dispenser**

### **1.1 Problem Restated**

Medication non-adherence causes \~125 k US hospital deaths/year and billions in avoidable costs. Elderly and chronically ill patients struggle with getting their medications on time

**1.2 Landscape Scan**

1. Commercial Options  
   1. Hero  
      1. Proven market demand  
      2. HIPAA dashboards  
      3. Not very cost efficient  
         1. Costs the user over $500 every year  
      4. No refill sensing  
2. SPEC 2.0 Smart Pill Expert System  
   1. IoT dispenser that release dose at scheduled times  
   2. Gaps:  
      1. Still required user confirmation  
         1. False positive “Taken” events

**1.3 Key Technical Findings**

- Dispensing accuracy  
  - Optical pill counting usually beats weight based methods especially when pills are less than 1g  
- Sensors  
  - HX711 load cell amplifier is the industry staple  
- Connectivity  
  - BLE \+Wi-Fi dual stack module  
  - Must meet home healthcare requirements for mains isolations

### **1.4 Feasibility Snapshot**

- Complexity:Medium  
- Expected cost:  
  - $85 without enclosure  
- Something cool to add  
  - Refill-level weight trending

**1.5 Next Steps**

- Look into how the HX711 driver works and figure out the main parts for how its needed to be implemented  
- Look into the tolerance analysis for all the components needed for this project  
- Look into the design we should implement

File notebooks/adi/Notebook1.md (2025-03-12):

# Notebook 1

**Date:** January 25th, 2025

## Objectives
1. Find a project to work on
2. Perform market analysis on the project idea
3. Write up the RFA

## Record of Work
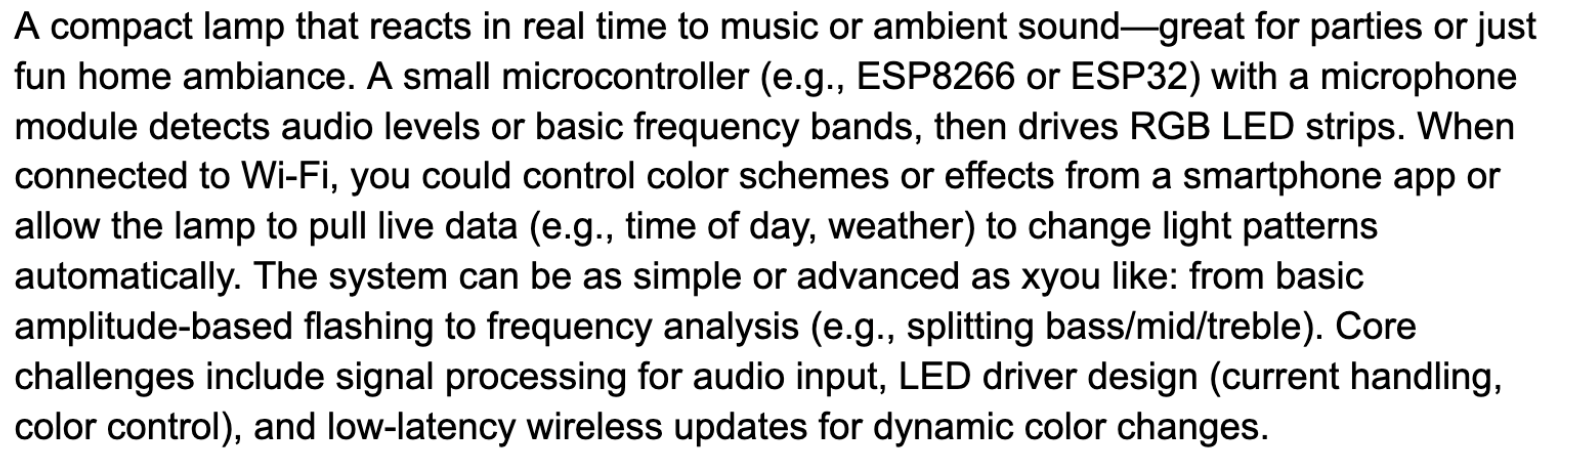
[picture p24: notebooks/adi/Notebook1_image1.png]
Idea 1

Idea 2

Idea 3: Smart Glasses for Visually Impaired

Problem: Visually impaired people can't tell where sounds come from in group settings.

Solution: Smart glasses that tell the wearer which direction a voice is coming from.

Key features:
1. Microphones on the glasses to detect sound direction
2. Vibration feedback on the side where sound comes from
3. Optional LEDs for those with some vision
4. Rechargeable battery in the frame

Benefits: Helps users face the person speaking, making social interactions easier.

Idea 4

## Personal Thoughts
Overall this class is really exciting. Our whole team looks like is working really well, and we are all pretty ambitious about our goals. I am worried about the feasibility of the projects though, since we are limited by time and budget. I do think we can learn most of the things we need to know. We should probably start studying up on KiCAD past the point of the CAD assignment, since it seems to be the main tool of this class. Soldering was hard so, I won't be taking the lead there.

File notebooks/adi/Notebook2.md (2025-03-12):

# Notebook 2

**Date:** February 8th, 2025

## Objectives
1. Determine the different subsystems required to build the project
2. Find similar products or subsystems already implemented to determine the different mechanical subsystems
3. Finalize a design for the solution and the general parts needed for that solution 

## Record of Work

### Subsystems
Block Diagram

#### Subsystem 1
The RTC timekeeps when to dispense the medications according
to the schedule set by the user. It maintains accurate time even during power outages through its backup
battery system. The module communicates with the microcontroller to
provide current-time data.

#### Subsystem 2
The ESP8266 enables WiFi and remote management of the dispenser. It runs a web
server that hosts the UI for medication management and provides real-time status
updates. The module allows users to receive notifications. It processes HTTP requests
for schedule updates and transmits dispenser status data to the cloud.

#### Subsystem 3
The microcontroller drives the stepper motors that rotate the dispensing cylinder. It will
make sure that the pills were dispensed at the right time (aka did you take your
medication). The microcontroller activates buzzers or speakers for audible notifications
and LEDs for visual alerts when it is time to take medication. Using ESP8266, the
microcontroller connects to a web app to send reminders, allow remote monitoring, and
enable users to adjust schedules.

#### Subsystem 4
The weight sensor system uses load cells and an HX711 amplifier to measure
medication quantities. It monitors the weight of each medication compartment to track
pill counts and verify successful dispensing. The sensor data is used to detect when
medications are running low and trigger refill alerts.

#### Subsystem 5
The device housing and mechanical components are fabricated using food-safe PLA or
PETG filament. The design includes separate sealed compartments for each medication
type, a rotating dispensing mechanism, and channels for pill routing.

#### Subsystem 6
The top of the device will consist of a funnel-like structure which will enable the user to
dispense the pill bottles one at a time. The funnels will drop the pills into a jar to sort
them into different placeholders. Once one kind of pill has been emptied, there will be a
disk in place to rotate onto the next jar for the next pill to be dispensed into. To have the
pills dispense properly we will have the top of the funnel open and close when it is ready
to take in a new pill, additionally, it will rotate the pillars so that it is directly below the
funnel, so we never lose pills in any sense.

### Visual Aid
Canva Drawing

## Personal Thoughts
The breakdown of this project seems to be something like power, mechanical, control, and interface. Although the underlying requirements are still not fleshed out. The HX711 and the ESP was the first few things we saw in terms of industry standards, but never heard or used them before. Also its been 5 years since I last worked on 3D printing, so that might become a bit too tough. We also need to start working on the documents, they need to be written well.

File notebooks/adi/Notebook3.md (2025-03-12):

# Notebook 3

**Date:** February 15th, 2025

## Objectives
1. Finalize a design to take to the machine shop
2. Determine how to have both power jack and backup battery
3. Create an example circuit, to learn more about KiCAD

## Record of Work
Design
Battery
Battery Backup Circuit
Example Circuit

## Personal Thoughts
First design on KiCAD is most certainly wrong. I just wanted to chalk something up just in case. The battery backup is worrying me, the battery would need to be rechargeable and just to charge it back up would be a whole 445 worthy project in itself. But, we need to figure out a solution to make this product work for the end user. I definately, need to go back and use labels for the circuit, it is awful otherwise. Also heavily considering removing ATmega and HC05 for ESP32.

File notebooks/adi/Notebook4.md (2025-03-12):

# Notebook 4

**Date:** February 25th, 2025

## Objectives
1. Create first PCB for PCB review
2. Find the exact parts needed
3. Determine which subsystems to demo for breadboard demo

## Record of Work
First PCB Schematic
First PCB

### TA Meeting Results for Demo:
1. Interface Subsystem (LEDs + Push button)
2. Power Subsystem (Backup battery + power jack)
3. Backup battery should charge up too
4. Mechanical Subsystem (servo motor / stepper motor)

### Battery To Buy
Battery Image 1
Battery Image 2

## Personal Thoughts
We are so behind. Correction. We WERE so behind. We didn't have our parts bought yet, nor ordered, we had to remake the whole PCB after the PCB review, and the battery backup still wasn't figured out. But this week and the weekend was the most productive ECE 445 week of our whole semester so far. We figured out the PCB luckily due to us practicing with KiCAD before hand. Using the self help drawers and supply center catalog we were able to switch our parts to easily available ones. We also found the battery backup wire on Amazon that reroutes and recharges for us. Lastly we were able to give our designs to the machine shop and actually get in queue (spot 36 but can be higher if we are first to give parts).

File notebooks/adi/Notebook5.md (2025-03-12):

# Notebook 5

**Date:** March 1st, 2025

## Objectives
1. Change parts to those we can find in the supply center and electronics shop
2. Change microcontroller to ESP32-WROOM
3. Build the Schematic, PCB, and Gerber Files

## Record of Work

### Parts List
Parts
Ordered Parts

### PCBWay Order 1
Schematic
PCB

## Personal Thoughts
Was able to buy and order the parts for the final demo. Was able to create the PCB for Order 1 in time, despite significant last minute changes. Honestly, just very relaxed right now. We need to make sure we stay up to date with the information the TA and the calendar has. CAN NOT fall behind again.

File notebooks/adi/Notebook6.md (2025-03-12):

# Notebook 6

**Date:** March 5th, 2025

## Objectives
1. Complete Breadboard Demo Set Up
2. Create New PCB
3. Deliver Parts to Machine Shop

## Record of Work

We are second in line to have our machine built according to Gregg.

### Breadboard
Breadboard View 1
Breadboard View 2

### Second Round PCB
1. We need Reset and Boot buttons on the PCB
2. We need lower ohm resistors
3. We need to have the capacitors closer to the actual parts
New Schematic
New PCB

## Personal Thoughts
Breadboard demo went really well. We were working on the button starting bluetooth pairing for the longest time. Most of our code and circuit will be scrapped, but just need to prove functionality, which we did. I think the Prof. liked it. Looking forward to 3D printing some parts after spring break and actually soldering the PCB from order 1. No big updates. Need to tweak schematic for PCB 2.

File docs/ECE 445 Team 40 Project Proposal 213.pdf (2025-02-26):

### caTeam (#40) Members:

Aditya Perswal (apersw2)

Aryan Gosaliya (aryanag2)

Aryan Moon (aryanm7)

# Smart Medical Pill Dispenser

# ECE 445

## Project Proposal

February 10th, 2025

TA: Jiankun Yang

# Introduction

## Problem:

According to Census, (https://www.census.gov/library/stories/2024/06/metro-areas-population-age.html) the growth of the 65+ population is rapidly increasing seeing a 9.4% increase from 2020 to 2023. With people living longer lives, there are a few growing pains; largely medical troubles. With 54% of 65+ year olds taking four or more prescription drugs (KFF) (https://www.kff.org/affordable-care-act/issue-brief/data-note-prescription-drugs-and-older-adults/) and 50% forgetting to take them on time, or at all, (NIH) (https://pmc.ncbi.nlm.nih.gov/articles/PMC3068890/) we believe the way towards a healthier future for the growing post-retirement population, lies in automated medicine. Not only will this lead to healthier outcomes, but also major cost savings as the average 65+ year old spends around $800 per year (HPI Georgetown University). (https://hpi.georgetown.edu/rxdrugs/) Currently, there are a few options in the market to automate taking and preparing the concoctions of medications a patient must take per week but they range from largely useless to extremely expensive. Pill organizers play the role of “meal prepping” for medication, however, not only do they become a chore but also depend on the user placing the right medication into the right compartment the right amount of times. Notice the number of “rights” needed for a pill organizer to work and consider the error rate of a pharmacist, a professional, being 1.6% (NIH), (https://pubmed.ncbi.nlm.nih.gov/37848350/) it slowly becomes obvious that automated pill dispensers are a necessity. However, this leads to the second leg of the problem, automated pill dispensers like Hero (https://herohealth.com/subscription/fe440182-5856-4081-a953-eecbea376dd7/) cost $540 per year and only work with 2.4 GHz WiFi. With 10.9% of 65+ year olds living in poverty (Census) (https://www.census.gov/library/stories/2023/12/poverty-rate-varies-by-age-groups.html) and pills needing to be dispensed even during WiFi outages, it becomes clear that a solution that does not require internet and is cost-effective is a necessity.

## Solution:

To solve the problem/s listed above we propose a simple solution. A cost-effective ($250) automated pill dispenser that takes in 4 types of pills, needs to be connected to the internet only during calibration and any updates made by the user, and requires a far more cost-effective monthly server charge ($5/month). Our smart medical pill dispenser will take in user’s pills from the top in a funnel, one bottle at a time, and place them into their own compartments. After all (max 4 types) pills have been placed into the dispenser the user will navigate through a setup process that will ask them for the time, quantity, and type of pill they must take on any given day. The user will then be alerted via a web app (when connected by Bluetooth) and an LED as to when they must take their pills. Users will also be alerted of refills needed and if they forgot to take their medication. Lastly, the system will have an internal battery along with a charging brick to withstand power outages and will be allowed to update timing based on Bluetooth. The system automatically sorts pills into correct daily doses and dispenses them at the scheduled time, put simply.

## Visual Aid:


Figure 1: Visual Aid
As shown in Figure 1, the smart medical pill dispenser (SMPD) has a funnel at the top to compartmentalize different pills and a funnel at the bottom to dispense them all at once into the container of choice. Additionally, there is a plug for the tool, however, it is backed up with a battery to ensure proper dispensing even during outages. The phone is the main interface with which the user can customize their SMPD, with the program interface changing depending on whether the user is accessing the device through the internet or Bluetooth. Lastly, there are 3 LEDs on the device, one to indicate refills needed, another to indicate active dispensing, and last to indicate when a user has forgotten to take their pills. The PCB inside the SMPD will determine which pills are supposed to be dispensed based on the user-set configuration.

## High-Level Requirements:

Our project will be a success under the following constraints as mentioned in the RFA:

- 98.4% Pill Dispensing Accuracy
- The SMPD alerts the user within 5 seconds of the scheduled times
- Refill alerts are sent out when the compartment is left with ~10% of pills

# Design

## Block Diagram:


Figure 2: Block Diagram

## Subsystem Overview:

### Power Subsystem

This system will be using a 7812 voltage regulator to ensure a stable 12V DC output. The regulator will step down an input voltage of 14V DC to 12V DC, possible since a 7812 has a 2V dropout voltage, ensuring consistent power distribution for the microcontroller and all other components. A rechargeable 12V battery will serve as a backup power source, ensuring at least 24 hours of operation in case of a power failure. Essentially we are creating a voltage regulator that switches from an electrical outlet to a battery pack when the power goes out. These specifics are subject to change as we create the system, as this would be our first time creating such a circuit.

The charging circuit will include:

- Diode D1 (1N4007) to prevent reverse voltage flow into the regulator.
- Resistor R2 (100Ω) to limit the charging current to the battery.
- Diode D2 (1N4007) to avoid battery discharge back into the system.
- R1 (1kΩ) and an LED to indicate the power status of the system

### Control Subsystem

The microcontroller (MCU) will execute pill dispensing operations and ensure that the pills are dispensed at the right time. This subsystem will include a Real-Time Clock (RTC) component to work with the MCU so that the SMPD dispenses at the right time, with a maximum drift of ~1 minute per month. The MCU will also process user input from the web app through a Bluetooth connection and control the stepper motors responsible for pill dispensing. To ensure reliability, the power subsystem will automatically switch from electrical outlet to battery.

It works with:

- The mechanical subsystem to trigger pill sorting and dispensing.
- The interface subsystem for user notifications and inputs.
- The power subsystem for stable operation.

### Mechanical subsystem

The pill sorting system will use a stepper motor-driven rotating disk to align pill compartments with the dispensing and intake funnels. This mechanism is designed to achieve a sorting accuracy of 98.4%, which is equivalent to a pharmacist.

To dispense pills, motor-controlled gates at the bottom will release the precise number of pills per dose, as scheduled by the user. Load sensors will track pill levels, triggering refill alerts when the compartments reach ~10% capacity (+/- 0.9%).

This subsystem is essential for meeting the accuracy requirements and ensuring timely dispensing.

It works with:

- The control subsystem for activation and dose scheduling.
- The interface subsystem for user alerts and notifications.

### Interface subsystem

The user interface will consist of a Bluetooth connected web app, allowing users to configure their pill schedules and receive notifications. Additionally, the physical user input button will be included for basic interactions such as setup mode and manual dispensing, changing functionality based on which mode it is in.

- The system will use LED indicators to provide real-time status updates:
- Refill Needed (Yellow LED): Alerts the user when pill levels drop below ~10%.
- Active Dispensing (Green LED): Indicates when a scheduled dose is being dispensed.
- Missed Dose Alert (Red LED): Notifies the user within 5 seconds of a missed scheduled dose.
- The LED brightness must be visible in daylight at a distance of 1 meter for accessibility.

This subsystem works with:

- The control subsystem for status updates and notifications.
- The power subsystem for reliable operation.

## Sorting Mechanism

Objective:

The system must correctly separate and store up to four pill types, ensuring at least 98.4% sorting accuracy while minimizing user input.

### How the Sorting Mechanism Works

### 1. Pill Loading Process (Manual but Guided)

- The top section of the device has one funnel. As the user rotates through their pill bottles the compartments for the pills rotate under the funnel.
- The user loads one pill bottle at a time into Compartment 1 and presses the main button which constitutes “Next” during configuration mode.
- The system then rotates a mechanical disk (via a stepper motor) to align the next empty compartment under the intake funnel.
- The process repeats for up to four different pills.

### 2. Compartmentalization and Storage

- Each funnel leads to a separate storage chamber inside the dispenser.
- Once the loading process is complete, each pill type is stored in its respective compartment.
- The device then switches to dispensing mode, where pills are released as per the user’s scheduled dosages.

### Pill Dispensing Process

### 1. Scheduled Dispensing

- When it’s time to take the medication, the microcontroller activates stepper motors to release pills from the correct compartments.
- Each compartment has a gate-controlled release mechanism, ensuring that only the exact prescribed number of pills is dispensed.
- Pills drop through a final bottom-funnel into a small container for collection.

### 2. Tracking Pill Usage & Refill Alerts

- A weight sensor (load cell + HX711 amplifier) tracks the remaining pills.
- When the stock falls below a threshold, the system activates an LED alert and notifies the user via the web app to refill the specific compartment.

Sorting Accuracy & Testing

Requirement:

Sorting accuracy must be ≥ 98.4%

Testing Approach:

- Run trials with 100 pills (10 times) of varying sizes and weights.
- Track how many are correctly sorted into their compartments.
- If 984+ pills are correctly placed, the system meets the requirement.

Error Handling:

- To account for misidentification the SMPD will ask the user to confirm the correct pills were dispensed.
- If pills jam, the stepper motor reverses briefly and attempts to retry sorting.

Failure Considerations & Backup Mechanism

1. The sorting system halts safely since an RTC module maintains timing.
2. A backup battery ensures that the sorting function resumes when power returns.
3. The RTC also ensures that the pills continue to be dispensed at the right time.
4. The Bluetooth component will allow connection even if the power is out.

### Why This Approach?

Cost-Effective:

Using weight sensors instead of cameras reduces costs. Using 3d printing significantly reduces the costs of the chassis.

Compact & Scalable:

The rotating disk allows for a small form factor while enabling pill expansion in future iterations.

Minimal User Effort:

Users only need to pour pills; no manual sorting is required.

## Tolerance Analysis:

1. Pill Recognition Accuracy
a. The sorting system must achieve an accuracy of at least 98.4% as stated before
b. We will be conducting 10 trials with 100 pills each taking into consideration different sizes and weights ensuring that 984/1000 pills are sorted correctly
c. Potential sources of error include jamming or misalignment in the rotating disk, which will be solved by stepper motor reversal logic.
2. Power Consumption Calculations
a. Power consumption breakdown
i. Microcontroller ~ 50mW
ii. | Stepper Motors ~ 1 W
iii. | Sensors and LEDs ~ 50mW
iv. | Bluetooth module ~ 300mW
b. A 12 V rechargeable battery will sustain operation for at least a full day in standby mode.
3. Timing Precision Requirements
a. The RTC must maintain an accuracy of less than 1-minute drift per month
b. The pill dispenser should notify the user within 5 seconds of the scheduled time
c. Bluetooth latency should remain below 1 seconds to ensure real-time connectivity.
4. Storage Capacity Requirements
a. Each compartment holds up to 100 pills
b. Total storage: 400 pills (4 compartments)
c. Minimum threshold for refill alert: 10 pills per compartment
5. Error Rate in the Dispensing Mechanism
a. Stepper motors (NEMA 14) ensure precise movement
b. Load cell (HX711) tracks exact pill count
c. Error mitigation:
i. Pill jamming detection using load variance
ii. | Motor reversal logic for clearing jams
iii. | User confirmation for wrongly dispensed pills

# Ethics and Safety

As for ethics and safety, our team is going to ensure the product is safe to use and HIPAA compliant. This will require that the device be made with food-safe PLA or PETG filament as we plan to 3d print it. Additionally, the cloud infrastructure we build will need to remain HIPAA compliant by only using GCP/AWS/Azure’s HIPAA-focused services. We will continuously document our development process to ensure any 3rd party can verify our statements. Additionally, we are guided by the ethical guidelines as written in the IEEE Code of Ethics (https://www.ieee.org/about/corporate/governance/p7-8.html) and ACM Code of Ethics. (https://www.acm.org/code-of-ethics) Our entire team has also completed the University’s Division of Research Safety’s safety training. (https://shibboleth.research.illinois.edu/V2/EDS/Default.aspx) We have also read through the safe battery usage (https://courses.grainger.illinois.edu/ece445/documents/GeneralBatterySafety.pdf) and safe current limits (https://courses.grainger.illinois.edu/ece445/documents/Safe_Current_Limits.pdf) guidelines. We will treat everyone with respect and kindness, showcasing empathy and understanding. Our team will ensure that our project is built to strict networking safety guidelines, to ensure no user data can be stolen, and comply with any relevant licensing terms for all the software we use. Lastly, we will ensure that any training needed in the future is taken immediately and with the utmost focus.

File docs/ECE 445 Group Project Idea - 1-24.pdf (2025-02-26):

# Smart Medical Dispenser & Sorter

The Problem: People often struggle with two major medication challenges. First, they forget to take their medications at the right time or take incorrect amounts. Second, they must spend considerable time sorting multiple medications into daily doses, which is both time-consuming and prone to errors. This is especially difficult for elderly patients or those with multiple prescriptions who must organize dozens of pills each week.

The Solution: An intelligent device that both sorts and dispenses medications automatically. Instead of manually organizing pills into compartments, users simply load entire bottles of medication one at a time into the device. The system then automatically sorts these pills into correct daily doses and dispenses them at scheduled times. Everything is controlled through a simple website where users or caregivers can set schedules and monitor medication adherence.

How It's Made: The heart of the system is a custom-designed circuit board built around an ATmega2560 microcontroller, which orchestrates all operations. The device consists of two main chambers: a sorting section and a dispensing carousel, housed in a secure plastic enclosure with separate compartments for electronics and medications.

The sorting mechanism operates like an automated assembly line in miniature. When a user loads a bottle of pills, they first tell the system which medication it is through the website. The pills enter a vibrating feed channel that ensures they move one at a time. Each pill passes through an infrared sensor gate that counts and verifies each pill individually. A rotating sorting arm, powered by a precise stepper motor, then places each pill into the correct compartment of the dispensing carousel below.

The dispensing carousel is driven by its own stepper motor and contains compartments for each scheduled dose. An optical sensor ensures perfect alignment when rotating to dispense medications. When it's time for a dose, the system alerts the user through both the device (with lights and sounds) and the website (with notifications).

The electronic brain coordinates everything through a Wi-Fi connection established by an ESP8266 module. This allows the system to receive scheduling information and send status updates to the web interface. A real-time clock chip ensures accurate timing even if the internet connection is temporarily lost. The entire system runs on a regulated power supply with battery backup to prevent any interruption in service.

For safety, multiple verification systems are in place. Infrared sensors count each pill to ensure accurate sorting. A lid switch detects any unauthorized access attempts. The software keeps track of all medications and quantities, warning users when supplies run low. If there's ever a power or mechanical issue, a manual override system allows access to medications in an emergency.

The web interface provides an intuitive way to set up and monitor the system. Users can input their medication schedules, specify which medication is being loaded, view their dispensing history, and receive alerts about low medication levels or missed doses. This information can also be shared with caregivers or healthcare providers if desired.

# Smart Parking Assistant w/ Display

The Problem: Many drivers struggle with parking in tight spaces and gauging distances to obstacles, especially in older cars without built-in sensors. Traditional parking sensors are either expensive to install or provide only basic beeping feedback.

The Solution: A standalone, easy-to-install parking assistant that shows exact distances on a small display. It mounts on your dashboard and connects to ultrasonic sensors on your rear bumper. When you're in reverse, it shows you exactly how many feet/inches you are from obstacles.

How It's Made: The system consists of three main parts that can be built in 3 weeks:

Core Components:

- Arduino Nano (main controller)
- 3 ultrasonic sensors (HC-SR04)
- Small OLED display
- Buzzer for audio feedback
- 12V to 5V car power adapter
- Simple PCB for connections

The system taps into the car's reverse light for power and activation. When you put the car in reverse, the system automatically turns on, displaying distances from left, center, and right sensors. The display shows actual numbers (like "2.5 feet") rather than just beeping.

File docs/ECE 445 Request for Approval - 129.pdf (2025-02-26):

# Smart Medical Pill Dispenser (SMPD)

Team Members:
- Aditya Perswal (apersw2)
- Aryan Gosaliya (aryanag2)
- Aryan Moon (aryanm7)

## Problem

People often struggle with two major medication challenges. First, they forget to take their medications at the right time or take incorrect amounts. Second, they spend time sorting multiple medications into daily doses, which is both time-consuming and prone to errors. This is especially difficult for the elderly with multiple prescriptions they organize each week.

## Solution

An intelligent device that both sorts and dispenses medications automatically. Instead of manually organizing pills into compartments, users simply load entire medication bottles one at a time into the device. The system then automatically sorts these pills into correct daily doses and dispenses them at scheduled times. You can use a website connected to your device's ID and place in the times, dosages, and days you need to dispense medications and the SMPD will buzz at those times and on clicking dispense give you the correct dosages at once.

## Solution Components

Subsystem 1
The RTC module provides precise timekeeping to dispense the medications according to schedule. It maintains accurate time even during power outages through its backup battery system. The module communicates with the microcontroller via I2C protocol to provide current-time data.

Subsystem 2
The ESP8266 enables WiFi and remote management of the dispenser. It runs a web server that hosts the UI for medication management and provides real-time status updates. The module allows users to receive notifications. It processes HTTP requests for schedule updates and transmits dispenser status data to the cloud.

Subsystem 3
The microcontroller drives the stepper motors that rotate the dispensing cylinder. It will make sure that the pills were dispensed at the right time (aka did you take your medication). The microcontroller activates buzzers or speakers for audible notifications and LEDs for visual alerts when it is time to take medication. Using ESP8266, the microcontroller connects to a web app to send reminders, allow remote monitoring, and enable users to adjust schedules.

Subsystem 4
The weight sensor system uses load cells and an HX711 amplifier to measure medication quantities. It monitors the weight of each medication compartment to track pill counts and verify successful dispensing. The sensor data is used to detect when medications are running low and trigger refill alerts.

Subsystem 5
The device housing and mechanical components are fabricated using food-safe PLA or PETG filament. The design includes separate sealed compartments for each medication type, a rotating dispensing mechanism, and channels for pill routing.

Subsystem 6
The top of the device will consist of a funnel-like structure which will enable the user to dispense the pill bottles one at a time. The funnels will drop the pills into a jar to sort them into different placeholders. Once one kind of pill has been emptied, there will be a disk in place to rotate onto the next jar for the next pill to be dispensed into. To have the pills dispense properly we will have the top of the funnel open and close when it is ready to take in a new pill, additionally, it will rotate the pillars so that it is directly below the funnel, so we never lose pills in any sense.

## Criterion For Success

The following are all True/False evaluations

1. The smart medical pill dispenser correctly buzzes at the right day and time
2. The smart medical pill dispenser correctly dispenses the right medication with the correct dosage
3. The smart medical pill dispenser automatically sorts the inputted bottles into separate compartments
4. The smart medical pill dispenser appropriately alerts users when they need a refill by determining when certain medications are about to run out

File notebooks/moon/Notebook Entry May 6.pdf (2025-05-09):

## Notebook 12

Date: 5/6/2025

Objectives:

1. Finish the mock demo

Record of Work:
Today was the big one—our final presentation. Honestly, walking in we were a little on edge, but mostly excited to finally show off what we’ve built. After all the late nights, scrambling to fix PCBs, and debugging code right before deadlines, we made it.

The presentation itself went really well. Everyone on the team did a solid job explaining their parts. We covered all the main components—control system, power, mechanics—and kept the flow going smoothly. It felt good to finally talk about everything we’ve done, not just the technical stuff but the actual impact this could have.

The professor gave us useful feedback—some ideas for better security features and suggestions on how to make the system more user-friendly down the road. But overall, it was clear she was impressed with how far the project had come. That felt really good to hear. After we wrapped up, we all just kind of looked at each other and let out a breath. We’re done. It’s been a wild ride, and seeing it all come together like that made everything worth it.

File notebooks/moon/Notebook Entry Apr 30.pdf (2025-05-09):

## Notebook 10

Date: 4/30/2025

Objectives:

1. Finish the final PCB
2. Finish the Final Demo

Record of Work:

Our final demo went really well, and it was a huge relief to see everything come together after all the late nights and last-minute fixes. The device dispensed accurately, the LEDs flashed as expected, and the app interface ran without any hiccups. We could tell the demo resonated with the audience too—people seemed genuinely impressed with how polished the system looked and how reliably it performed.

At this point, the only piece left to finish is wiring the HX711 load cell amplifier onto the PCB. The version we used during the demo was external as it was on the breadboard, but we've already placed an order for the updated board that has dedicated space for it. Once it arrives, we’ll solder it on, run some calibration tests, and we should be good to go. Feels great to be at the finish line.

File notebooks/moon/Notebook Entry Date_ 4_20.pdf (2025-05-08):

## Notebook 9

Date: 4/20/2025

Objectives:
1. Finish Power only PCB
2. Switch to the Breakout Board
3. Do last PCB with through holes
4. Get the trimmers for the device

Record of Work:

We figured out he mistake with our trace widths and because we do have some time, we went ahead and ordered another PCB with the fixed trace widths. We know everything else is right in our PCB so this should work. We do need solder paste so we might get that from some store on campus. This is the last PCB design:


We also switched over to a breakout board instead as we kept running through micro USB ports breaking them every time as the solder is not strong enough. Another group told us this was fine


so we’re going with it. This is the breakout board we plan to use:

We have also designed trimmers for this device as the pills were not staying aligned and were jamming. This was something we were worried about but the machine shop assured it will not be a problem but now it is. This is the design for that:

We have 6 of these now costing about $1.57 and this will most definitely solve our issue.

Reflection:
When we tried powering the original PCB by feeding voltage through the regulator output through-holes, we ran into issues with only 1.7V at the 5V through-hole and 0.6V at the 3.3V one. We successfully tested the standalone power-only PCB, which is outputting solid values: ~5.1V and ~3.3V. Right now, the most stable plan is to keep the power subsystem on the dedicated PCB and run the rest of the system externally. Just hope the last PCB does get delivered on time

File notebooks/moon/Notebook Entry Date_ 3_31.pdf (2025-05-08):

## Notebook 8

Date: 3/31/2025

Objectives:
1. Finish the other PCB designs
2. Order more parts

Parts:
2N2222A - Transistor - Self Help Drawers

MBR1100 - Schottky Diode - Self Help Drawers

CP2102 - 5 done

ESP32-WROOM-32D - 10 done

ESP32-WROOM-32U - 5 done

Reflection:

We switched to a USB-to-UART bridge from the self-help drawers that’s easier to solder and more readily available. We're still a bit anxious about meeting PCB deadlines due to potential delivery delays happening in the class, so we placed another personal order to speed things up. On the bright side, our wiring and schematics are finally coming together smoothly, so overall progress has picked up.

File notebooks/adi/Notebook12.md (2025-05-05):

# Notebook 12

**Date:** May 4th, 2025

## Objectives
1. Finish Final Paper
2. Finish Final Presentation

## Record of Work
### Preparing for Mock Presentation
Zoom Call for Mock Presentation Prep

### Mock Presentation Notes
Communication Notes
Technical Notes

### Preparing for Final Presentation
In Person Meeting for Final Presentation Prep

### Final Paper Done
Final Paper is Done

## Personal Thoughts
Final demo let us know that we didn't have the right R&V table set up. We need to make sure that we talk about HOW we got our tests done and set up a correct procedure for it. The final paper will have all of that and our presentation will too. Mock presentation gave us a lot of great insight into how to get the presentation to be better and improve our communication skills. Final paper is largely done and we also got the extra credit video completed. Going to finish the semester off strong.

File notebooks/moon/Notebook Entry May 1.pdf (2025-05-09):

## Notebook 11

Date: 5/1/2025

Objectives:

1. Finish the mock demo

Record of Work:

We ran through our mock demo today, and overall it went really smoothly. The system worked as expected, and it was a great chance to practice our timing and transitions. It felt good to finally present something we were proud of and see it hold up under pressure.

The reviewers gave us some helpful feedback, mainly focused on presentation delivery. They pointed out that we should work on our posture while presenting, like standing more confidently and facing the audience instead of the screen. They also suggested cleaning up a few of our slides by reducing the amount of text and emphasizing key visuals or bullet points instead. We're planning to revise those slides this week and do another round of practice runs so that we're confident and polished for the real thing.

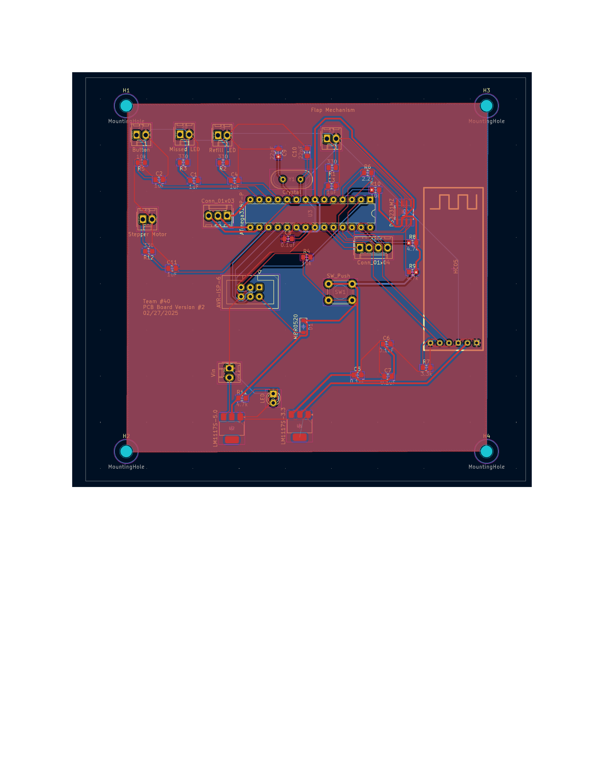
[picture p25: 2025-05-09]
notebooks/moon/pcb1 design.png

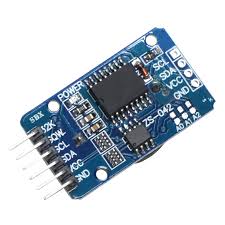
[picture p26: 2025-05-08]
notebooks/gosaliya/ds3231.jpeg

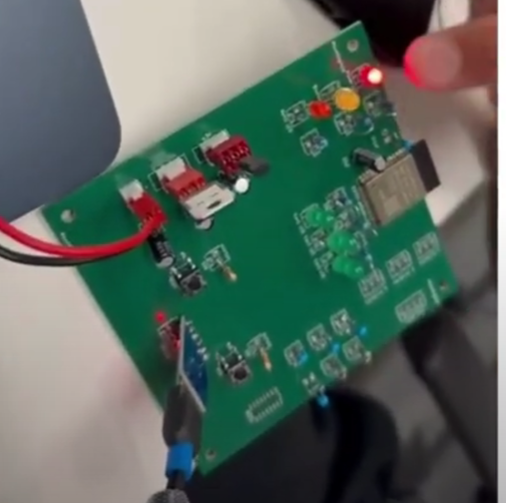
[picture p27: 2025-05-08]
notebooks/gosaliya/working-pcb.png

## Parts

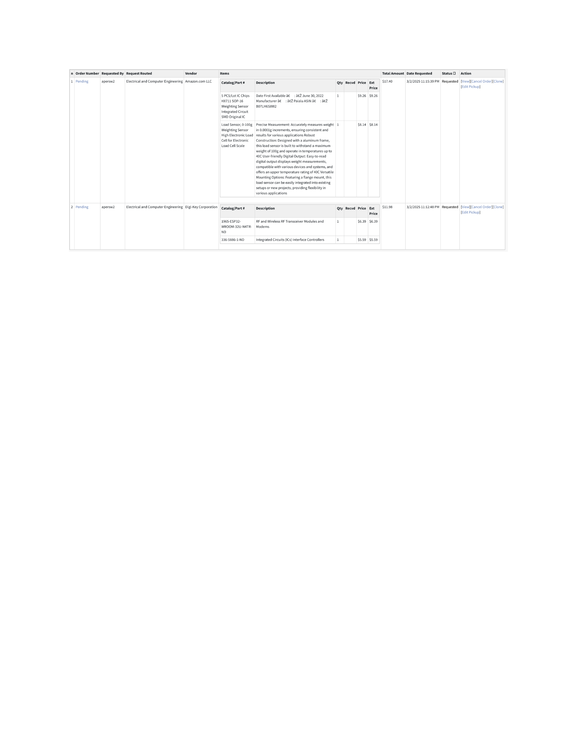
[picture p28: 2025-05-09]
notebooks/moon/eceb order.png

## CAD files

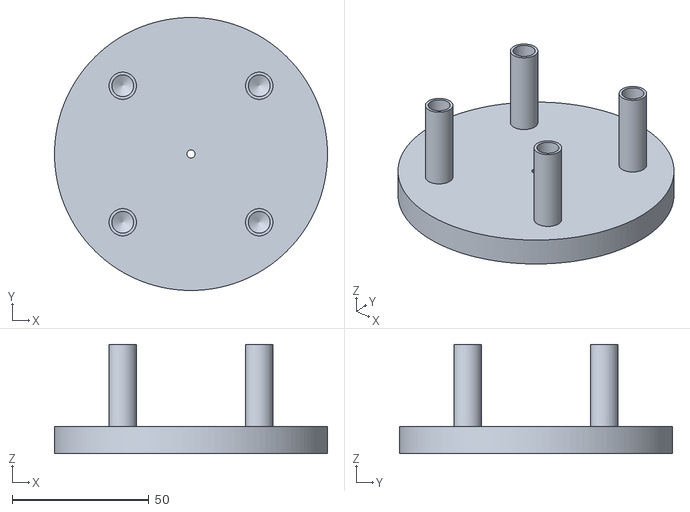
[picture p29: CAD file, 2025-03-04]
hardware/3D Models/Rotating Chamber-Body.stl
100.0 x 100.0 x 40.0

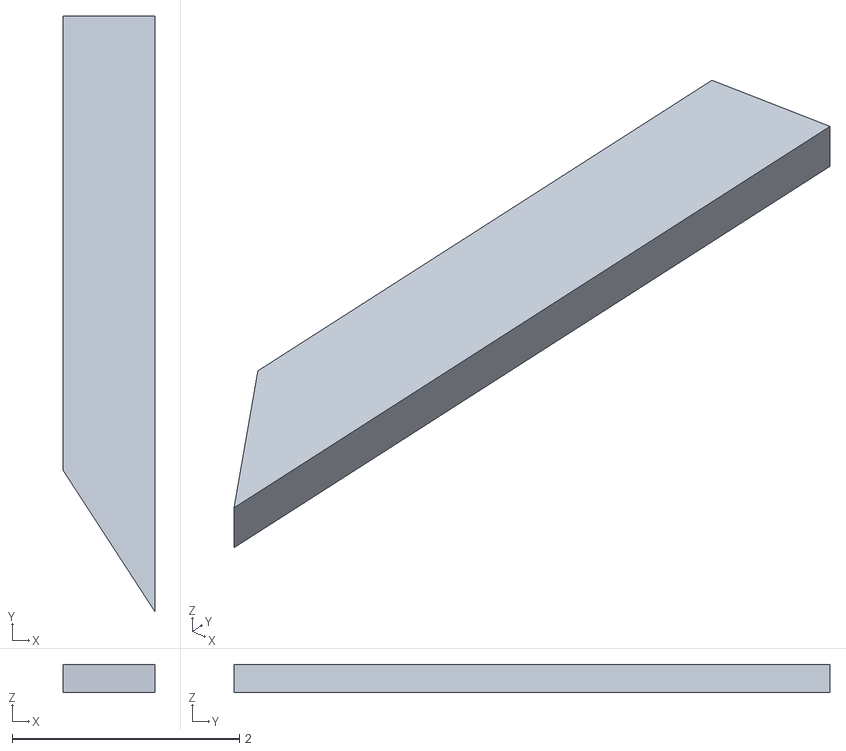
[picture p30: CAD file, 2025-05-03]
hardware/3D Prints/Compartment 2.stl
0.812 x 5.25 x 0.25

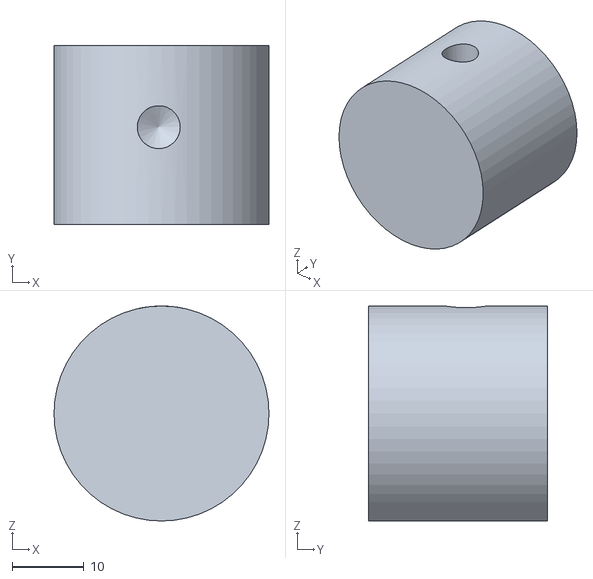
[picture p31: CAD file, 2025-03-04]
hardware/3D Models/Cavity Rotator-Body.stl
30.0 x 25.0 x 30.0

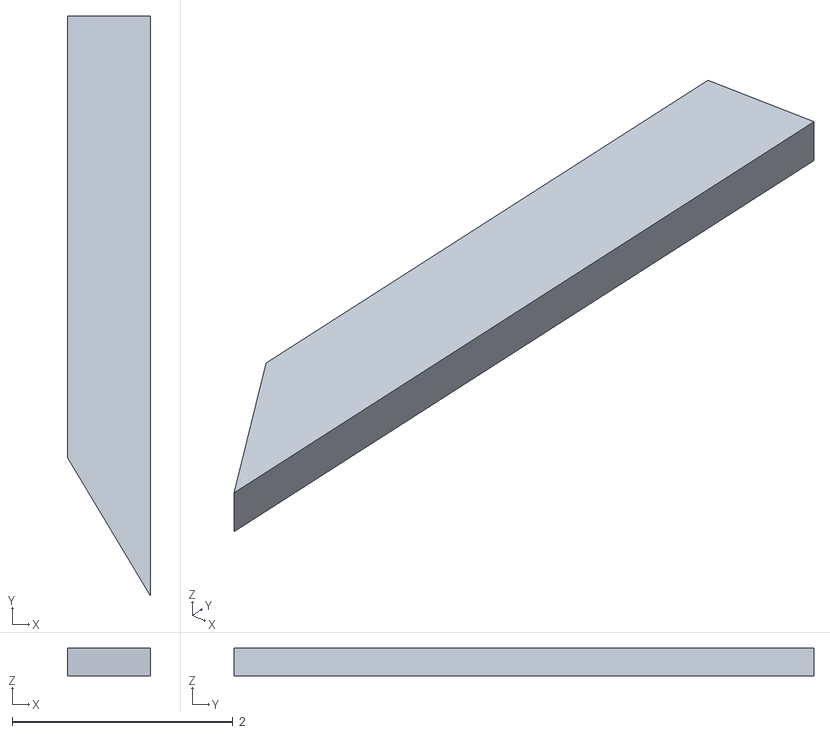
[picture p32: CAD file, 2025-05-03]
hardware/3D Prints/Compartment 3.stl
0.75 x 5.25 x 0.25

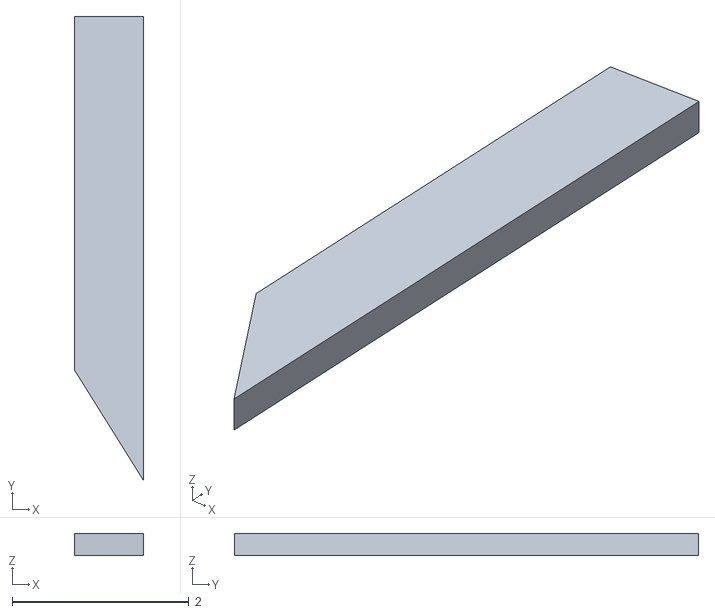
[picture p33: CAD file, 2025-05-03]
hardware/3D Prints/Compartment 1.stl
0.781 x 5.25 x 0.25

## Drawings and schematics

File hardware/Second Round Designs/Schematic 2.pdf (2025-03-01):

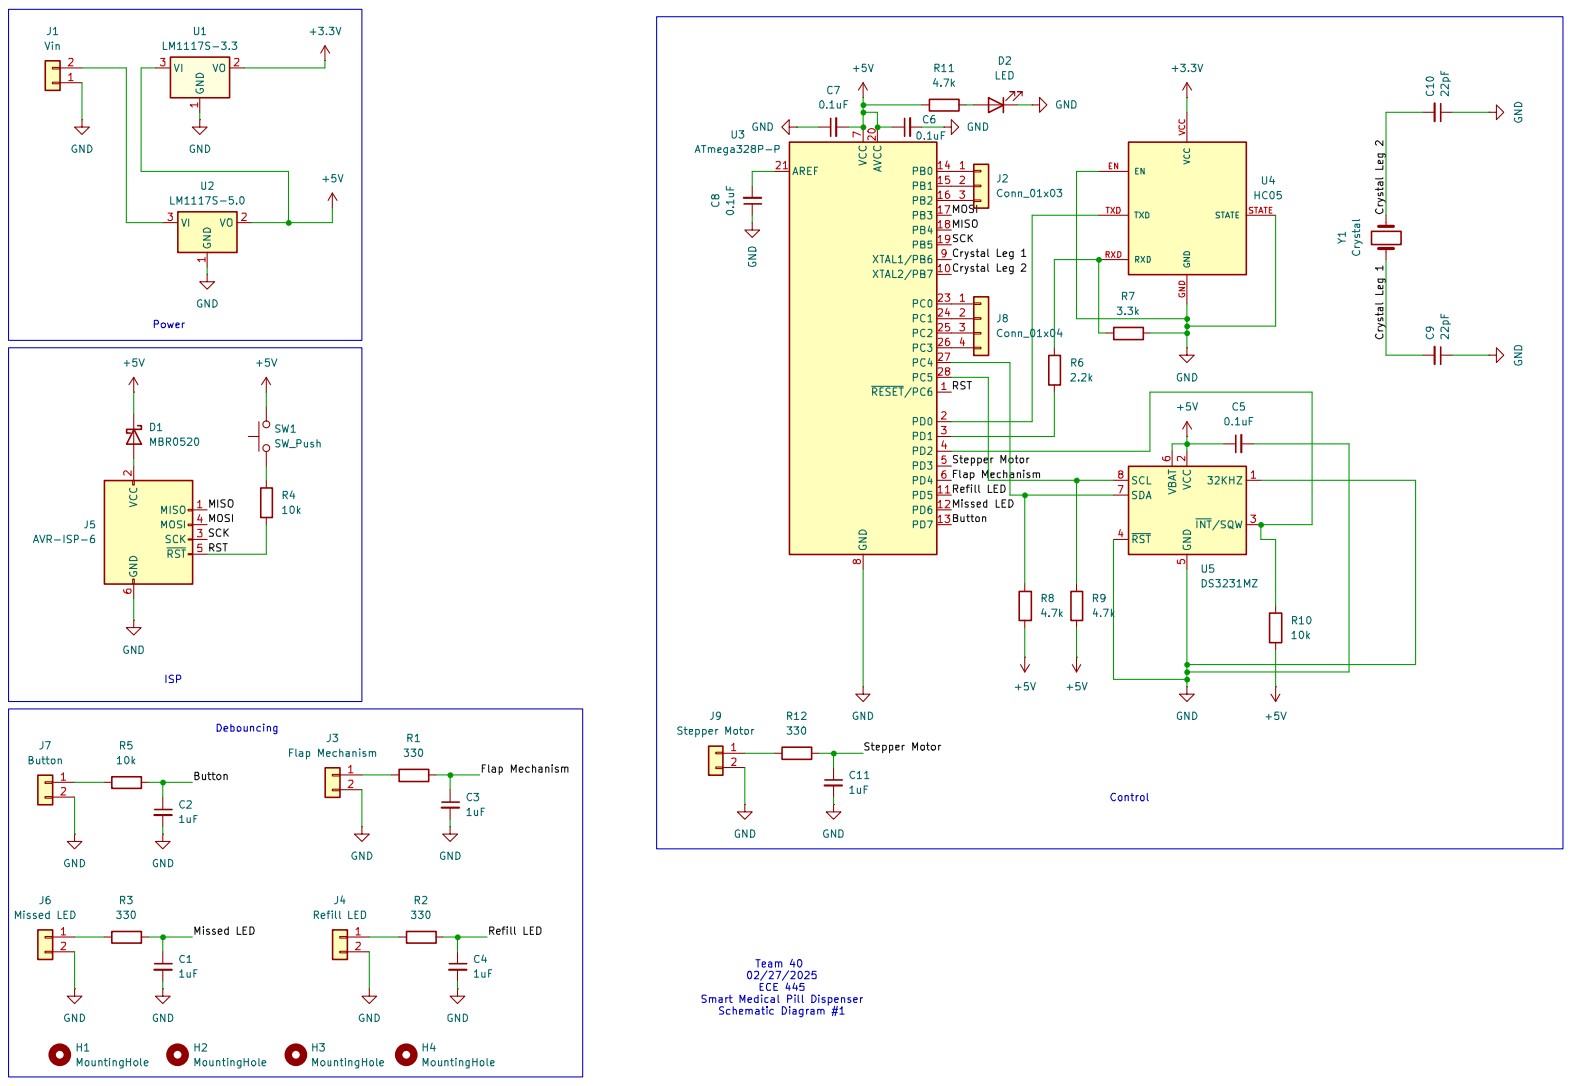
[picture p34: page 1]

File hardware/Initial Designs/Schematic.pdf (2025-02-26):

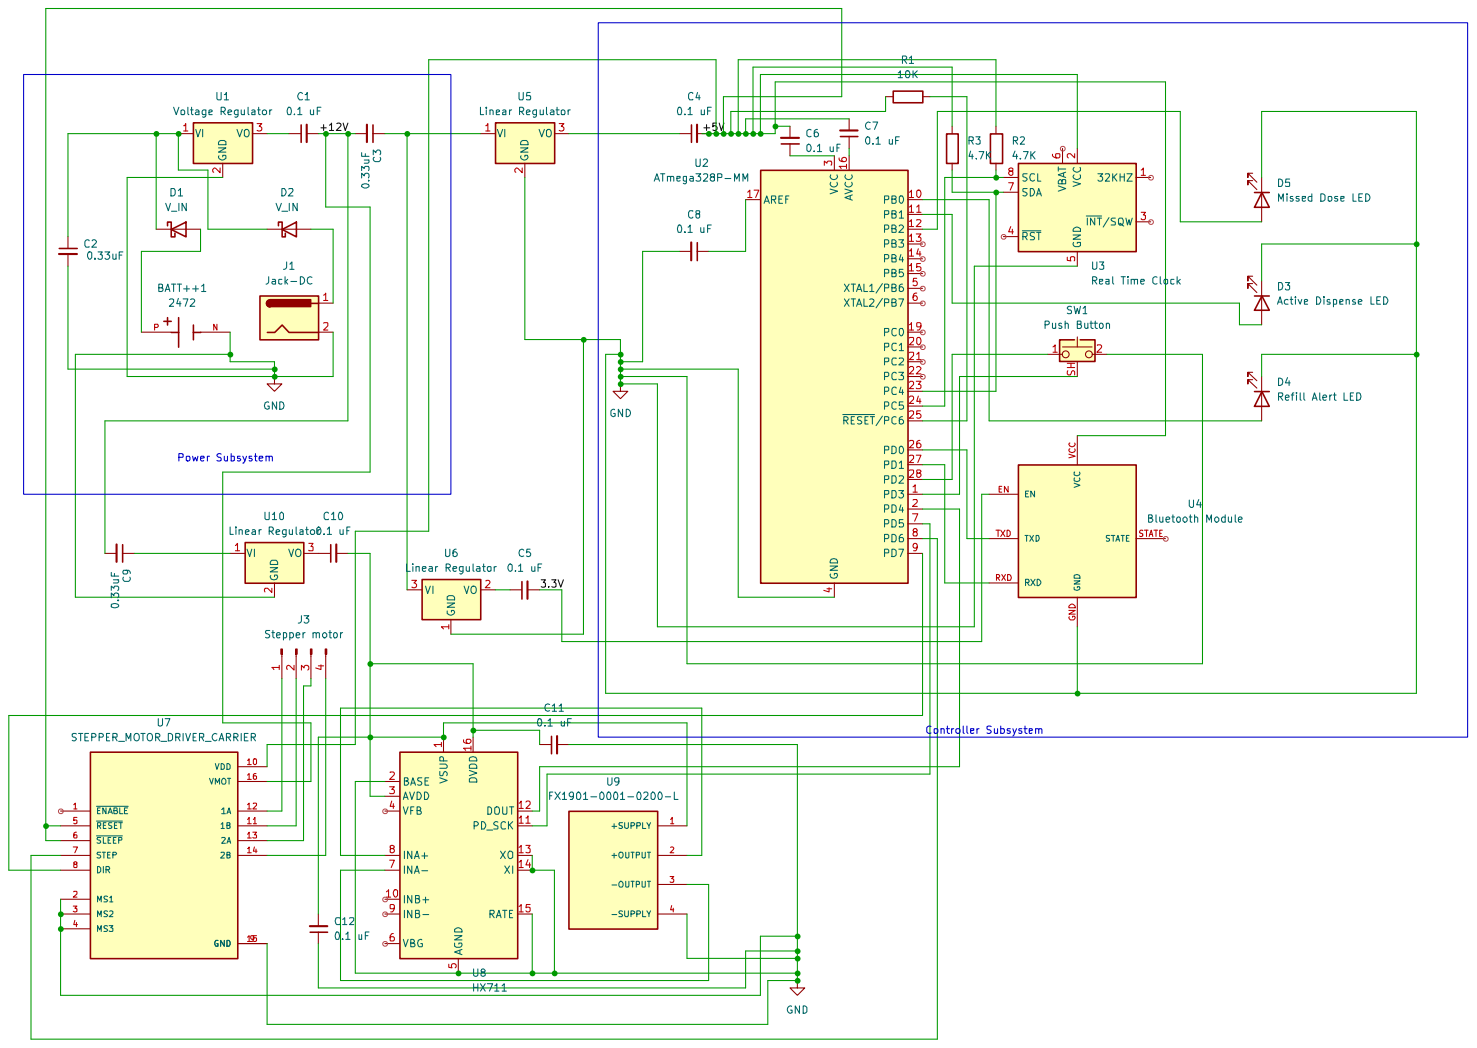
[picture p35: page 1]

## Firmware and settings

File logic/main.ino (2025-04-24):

#include <Arduino.h>
#include <ESP32Servo.h>
#include "HX711.h"
#include <BLEDevice.h>
#include <BLEServer.h>
#include <BLEUtils.h>
#include <BLE2902.h>
#include <time.h>
#include <Preferences.h>

#define SERVICE_UUID        "6e400001-b5a3-f393-e0a9-e50e24dcca9e"
#define CHAR_UUID_RX        "6e400003-b5a3-f393-e0a9-e50e24dcca9e"
#define CHAR_UUID_TX        "6e400002-b5a3-f393-e0a9-e50e24dcca9e"

Servo servo1, servo2, servo3;
const int servo1Pin = 22;
const int servo2Pin = 23;
const int servo3Pin = 25;

int servo1Pos = 0;
int servo2Pos = 0;
int servo3Pos = 0;

const int ledPin = 12;
bool ledState = false;

const int compartment1_LED = 13;
const int compartment2_LED = 14;
const int compartment3_LED = 16;
const int power_LED = 18;
const int refill_LED = 19;
const int bluetooth_LED = 27;

const int vibrationMotorPin = 26;
bool motorState = false;

const int LOADCELL_DOUT_PIN = 32;
const int LOADCELL_SCK_PIN  = 33;
HX711 scale;

BLECharacteristic *pTxCharacteristic;
bool deviceConnected = false;
bool isScanning = false;
unsigned long lastWeightUpdate = 0;
const unsigned long weightInterval = 5000;

struct tm timeinfo;
bool timeIsSynchronized = false;
unsigned long lastTimeCheck = 0;
const unsigned long timeCheckInterval = 2000;

bool hasDueSchedules = false;
unsigned long blinkInterval = 0;
bool bluetooth_LED_State = false;

#define MAX_SCHEDULES 20
Preferences preferences;
struct Schedule {
  bool active;
  int id;
  int hour;
  int minute;
  int daysOfWeek;
};
Schedule schedules[MAX_SCHEDULES];
int numSchedules = 0;

void addSchedule(int id, int hour, int minute, int daysOfWeek);
void clearSchedules();
void saveSchedules();
void loadSchedules();
bool checkSchedulesDue();
void alertScheduleDue();

bool dispensePending = false;
unsigned long lastServoActionTime = 0;
const unsigned long servoCompletionTimeout = 3000;
unsigned long lastDispenseCheck = 0;
const unsigned long dispenseCheckInterval = 2000;

bool servoMotionPending = false;
bool weightMeasurementNeeded = false;
unsigned long servoCompletionTime = 0;
const unsigned long servoSettlingTime = 1000;
const unsigned long servoOperationTimeout = 3000;

float calibrationWeight = 0.0614;
long calibrationReading = 0;
float calibrationFactor = 0.5;

bool isAutoCalibrating = false;
unsigned long calibrationStartTime = 0;
int calibrationStep = 0;
float knownWeightMg = 0;

float getFilteredWeight() {
  const int samples = 20;
  float readings[samples];
  float sum = 0;
  
  for(int i = 0; i < samples; i++) {
    readings[i] = scale.get_units(3);
    sum += readings[i];
    delay(5);
  }
  
  float average = sum / samples;
  
  float weight_mg = average * 1000;
  
  return weight_mg;
}

class MyServerCallbacks : public BLEServerCallbacks {
  void onConnect(BLEServer* pServer) override {
    deviceConnected = true;
    Serial.println("BLE Device Connected");
    
    digitalWrite(bluetooth_LED, HIGH);
    bluetooth_LED_State = true;
    
    isScanning = false;
    
    pTxCharacteristic->setValue("REQUEST_TIME");
    pTxCharacteristic->notify();
    
    pTxCharacteristic->setValue("REQUEST_SCHEDULES");
    pTxCharacteristic->notify();
    
    const char* helpText =
      "CMDs:\n"
      "SERVO1 OPEN/CLOSE\n"
      "SERVO2 OPEN/CLOSE\n"
      "SERVO3 OPEN/CLOSE\n"
      "VIBRATE ON/OFF\n"
      "COMP1_LED ON/OFF\n"
      "COMP2_LED ON/OFF\n"
      "COMP3_LED ON/OFF\n"
      "POWER_LED ON/OFF\n"
      "REFILL_LED ON/OFF\n"
      "BT_LED ON/OFF\n"
      "TARE\n"
      "RAW\n"
      "CALIBRATE:WEIGHT_IN_MG\n"
      "AUTO_CALIBRATE:WEIGHT_IN_MG\n"
      "SET_TIME:YYYY-MM-DD HH:MM:SS\n"
      "ADD_SCHEDULE:ID,HOUR,MINUTE,DAYS\n"
      "CLEAR_SCHEDULES\n"
      "SCHEDULE_DUE:true/false\n"
      "HELP";
    pTxCharacteristic->setValue(helpText);
    pTxCharacteristic->notify();
  }
  
  void onDisconnect(BLEServer* pServer) override {
    deviceConnected = false;
    Serial.println("BLE Device Disconnected");
    
    digitalWrite(bluetooth_LED, LOW);
    bluetooth_LED_State = false;
    
    servo1.write(175); servo1Pos = 180;
    servo2.write(168.5); servo2Pos = 180;
    servo3.write(175); servo3Pos = 180;
    digitalWrite(vibrationMotorPin, LOW); motorState = false;
    
    pServer->getAdvertising()->start();
    Serial.println("Advertising restarted");
    
    isScanning = true;
  }
};

class MyCallbacks : public BLECharacteristicCallbacks {
  void onWrite(BLECharacteristic* pCharacteristic) override {
    String rx = pCharacteristic->getValue();
    if (rx.isEmpty()) return;
    String cmd = String(rx.c_str());
    cmd.trim();
    Serial.print("Received command: ");
    Serial.println(cmd);
    
    if (cmd.startsWith("SET_TIME:")) {
      String timeStr = cmd.substring(9);
      Serial.print("Setting time to: ");
      Serial.println(timeStr);
      
      int year, month, day, hour, minute, second;
      sscanf(timeStr.c_str(), "%d-%d-%d %d:%d:%d", &year, &month, &day, &hour, &minute, &second);
      
      timeinfo.tm_year = year - 1900;
      timeinfo.tm_mon = month - 1;
      timeinfo.tm_mday = day;
      timeinfo.tm_hour = hour;
      timeinfo.tm_min = minute;
      timeinfo.tm_sec = second;
      
      timeIsSynchronized = true;
      
      pTxCharacteristic->setValue("OK: Time synchronized");
      pTxCharacteristic->notify();
      return;
    }
    
    if (cmd.startsWith("ADD_SCHEDULE:")) {
      String scheduleStr = cmd.substring(13);
      Serial.print("Adding schedule: ");
      Serial.println(scheduleStr);
      
      int id, hour, minute, days;
      sscanf(scheduleStr.c_str(), "%d,%d,%d,%d", &id, &hour, &minute, &days);
      
      addSchedule(id, hour, minute, days);
      
      pTxCharacteristic->setValue("OK: Schedule added");
      pTxCharacteristic->notify();
      return;
    }
    
    if (cmd == "CLEAR_SCHEDULES") {
      Serial.println("Clearing all schedules");
      clearSchedules();
      
      pTxCharacteristic->setValue("OK: All schedules cleared");
      pTxCharacteristic->notify();
      return;
    }
    
    if (cmd.startsWith("SCHEDULE_DUE:")) {
      String statusStr = cmd.substring(13);
      statusStr.trim();
      statusStr.toLowerCase();
      
      hasDueSchedules = (statusStr == "true");
      
      if (hasDueSchedules) {
        Serial.println("Medication schedule is due!");
        for (int i = 0; i < 3; i++) {
          digitalWrite(compartment1_LED, HIGH);
          digitalWrite(compartment2_LED, HIGH);
          digitalWrite(compartment3_LED, HIGH);
          delay(300);
          digitalWrite(compartment1_LED, LOW);
          digitalWrite(compartment2_LED, LOW);
          digitalWrite(compartment3_LED, LOW);
          delay(300);
        }
      } else {
        Serial.println("No schedules due");
      }
      
      pTxCharacteristic->setValue("OK: Schedule status updated");
      pTxCharacteristic->notify();
      return;
    }
    
    cmd.toUpperCase();
    
    if (cmd == "HELP") {
      const char* helpText =
        "CMDs:\n"
        "SERVO1 OPEN/CLOSE\n"
        "SERVO2 OPEN/CLOSE\n"
        "SERVO3 OPEN/CLOSE\n"
        "VIBRATE ON/OFF\n"
        "COMP1_LED ON/OFF\n"
        "COMP2_LED ON/OFF\n"
        "COMP3_LED ON/OFF\n"
        "POWER_LED ON/OFF\n"
        "REFILL_LED ON/OFF\n"
        "BT_LED ON/OFF\n"
        "TARE\n"
        "RAW\n"
        "CALIBRATE:WEIGHT_IN_MG\n"
        "AUTO_CALIBRATE:WEIGHT_IN_MG\n"
        "SET_TIME:YYYY-MM-DD HH:MM:SS\n"
        "ADD_SCHEDULE:ID,HOUR,MINUTE,DAYS\n"
        "CLEAR_SCHEDULES\n"
        "SCHEDULE_DUE:true/false\n"
        "HELP";
      pTxCharacteristic->setValue(helpText);
      pTxCharacteristic->notify();
      return;
    }
    
    if (cmd == "TARE") {
      scale.tare(20);
      Serial.println("Scale tared.");
      pTxCharacteristic->setValue("OK: Scale tared");
      pTxCharacteristic->notify();
      return;
    }
    
    if (cmd == "RAW") {
      long raw = scale.read_average(10);
      char buf[32];
      snprintf(buf, sizeof(buf), "RAW: %ld", raw);
      Serial.println(buf);
      pTxCharacteristic->setValue(buf);
      pTxCharacteristic->notify();
      return;
    }
    
    if (cmd.startsWith("CALIBRATE:")) {
      String weightStr = cmd.substring(10);
      float knownWeightMg = weightStr.toFloat();
      
      if (knownWeightMg <= 0) {
        String response = "Error: Invalid weight value. Format: CALIBRATE:WEIGHT_IN_MG";
        pTxCharacteristic->setValue(response.c_str());
        pTxCharacteristic->notify();
        return;
      }
      
      Serial.printf("Starting calibration with %.2f mg reference weight\n", knownWeightMg);
      
      calibrateScale(knownWeightMg);
      return;
    }
    
    if (cmd.startsWith("AUTO_CALIBRATE:")) {
      String weightStr = cmd.substring(15);
      float knownWeightMg = weightStr.toFloat();
      
      if (knownWeightMg <= 0) {
        String response = "Error: Invalid weight value. Format: AUTO_CALIBRATE:WEIGHT_IN_MG";
        pTxCharacteristic->setValue(response.c_str());
        pTxCharacteristic->notify();
        return;
      }
      
      Serial.printf("Starting automatic calibration with %.2f mg reference weight\n", knownWeightMg);
      
      startAutoCalibration(knownWeightMg);
      return;
    }
    
    if (cmd == "SERVO1 OPEN" && servo1Pos != 0) {
      servoMotionPending = true;
      servoCompletionTime = millis() + servoOperationTimeout;
      
      servo1.write(10);
      servo1Pos = 0;
      dispensePending = true;
      lastServoActionTime = millis();
      Serial.println("Compartment 1 Opened");
      
      weightMeasurementNeeded = true;
    } else if (cmd == "SERVO1 CLOSE" && servo1Pos != 180) {
      servoMotionPending = true;
      servoCompletionTime = millis() + servoOperationTimeout;
      
      servo1.write(175);
      servo1Pos = 180;
      dispensePending = true;
      lastServoActionTime = millis();
      Serial.println("Compartment 1 Closed");
      
      servoCompletionTime = millis();
      servoMotionPending = false;
    }
    
    if (cmd == "SERVO2 OPEN" && servo2Pos != 0) {
      servoMotionPending = true;
      servoCompletionTime = millis() + servoOperationTimeout;
      
      servo2.write(10);
      servo2Pos = 0;
      dispensePending = true;
      lastServoActionTime = millis();
      Serial.println("Compartment 2 Opened");
      
      weightMeasurementNeeded = true;
    } else if (cmd == "SERVO2 CLOSE" && servo2Pos != 180) {
      servoMotionPending = true;
      servoCompletionTime = millis() + servoOperationTimeout;
      
      servo2.write(168.5);
      servo2Pos = 180;
      dispensePending = true;
      lastServoActionTime = millis();
      Serial.println("Compartment 2 Closed");
      
      servoCompletionTime = millis();
      servoMotionPending = false;
    }
    
    if (cmd == "SERVO3 OPEN" && servo3Pos != 0) {
      servoMotionPending = true;
      servoCompletionTime = millis() + servoOperationTimeout;
      
      servo3.write(10);
      servo3Pos = 0;
      dispensePending = true;
      lastServoActionTime = millis();
      Serial.println("Compartment 3 Opened");
      
      weightMeasurementNeeded = true;
    } else if (cmd == "SERVO3 CLOSE" && servo3Pos != 180) {
      servoMotionPending = true;
      servoCompletionTime = millis() + servoOperationTimeout;
      
      servo3.write(175);
      servo3Pos = 180;
      dispensePending = true;
      lastServoActionTime = millis();
      Serial.println("Compartment 3 Closed");
      
      servoCompletionTime = millis();
      servoMotionPending = false;
    }
    
    if (cmd == "VIBRATE ON") {
      digitalWrite(vibrationMotorPin, HIGH);
      motorState = true;
      Serial.println("Vibration Motor Turned ON");
    } else if (cmd == "VIBRATE OFF") {
      digitalWrite(vibrationMotorPin, LOW);
      motorState = false;
      Serial.println("Vibration Motor Turned OFF");
    }
    
    if (cmd == "COMP1_LED ON") {
      digitalWrite(compartment1_LED, HIGH);
      Serial.println("Compartment 1 LED Turned ON");
    } else if (cmd == "COMP1_LED OFF") {
      digitalWrite(compartment1_LED, LOW);
      Serial.println("Compartment 1 LED Turned OFF");
    }
    
    if (cmd == "COMP2_LED ON") {
      digitalWrite(compartment2_LED, HIGH);
      Serial.println("Compartment 2 LED Turned ON");
    } else if (cmd == "COMP2_LED OFF") {
      digitalWrite(compartment2_LED, LOW);
      Serial.println("Compartment 2 LED Turned OFF");
    }
    
    if (cmd == "COMP3_LED ON") {
      digitalWrite(compartment3_LED, HIGH);
      Serial.println("Compartment 3 LED Turned ON");
    } else if (cmd == "COMP3_LED OFF") {
      digitalWrite(compartment3_LED, LOW);
      Serial.println("Compartment 3 LED Turned OFF");
    }
    
    if (cmd == "POWER_LED ON") {
      digitalWrite(power_LED, HIGH);
      Serial.println("Power LED Turned ON");
    } else if (cmd == "POWER_LED OFF") {
      digitalWrite(power_LED, LOW);
      Serial.println("Power LED Turned OFF");
    }
    
    if (cmd == "REFILL_LED ON") {
      digitalWrite(refill_LED, HIGH);
      Serial.println("Refill LED Turned ON");
    } else if (cmd == "REFILL_LED OFF") {
      digitalWrite(refill_LED, LOW);
      Serial.println("Refill LED Turned OFF");
    }
    
    if (cmd == "BT_LED ON") {
      digitalWrite(bluetooth_LED, HIGH);
      bluetooth_LED_State = true;
      Serial.println("Bluetooth LED Turned ON");
    } else if (cmd == "BT_LED OFF") {
      digitalWrite(bluetooth_LED, LOW);
      bluetooth_LED_State = false;
      Serial.println("Bluetooth LED Turned OFF");
    }
    
    if (cmd == "LED ON") {
      digitalWrite(bluetooth_LED, HIGH);
      bluetooth_LED_State = true;
      Serial.println("Bluetooth LED Turned ON (via legacy LED command)");
    } else if (cmd == "LED OFF") {
      digitalWrite(bluetooth_LED, LOW);
      bluetooth_LED_State = false;
      Serial.println("Bluetooth LED Turned OFF (via legacy LED command)");
    }
  }
};

void addSchedule(int id, int hour, int minute, int daysOfWeek) {
  for (int i = 0; i < numSchedules; i++) {
    if (schedules[i].id == id) {
      schedules[i].hour = hour;
      schedules[i].minute = minute;
      schedules[i].daysOfWeek = daysOfWeek;
      schedules[i].active = true;
      saveSchedules();
      return;
    }
  }
  
  if (numSchedules < MAX_SCHEDULES) {
    schedules[numSchedules].id = id;
    schedules[numSchedules].hour = hour;
    schedules[numSchedules].minute = minute;
    schedules[numSchedules].daysOfWeek = daysOfWeek;
    schedules[numSchedules].active = true;
    numSchedules++;
    saveSchedules();
  }
}

void clearSchedules() {
  numSchedules = 0;
  saveSchedules();
}

void saveSchedules() {
  preferences.begin("schedules", false);
  
  preferences.putInt("count", numSchedules);
  
  for (int i = 0; i < numSchedules; i++) {
    char key[16];
    sprintf(key, "sched%d", i);
    
    uint32_t data = schedules[i].id & 0x3F;
    data |= ((uint32_t)(schedules[i].hour & 0x1F) << 6);
    data |= ((uint32_t)(schedules[i].minute & 0x3F) << 11);
    data |= ((uint32_t)(schedules[i].daysOfWeek & 0x7F) << 17);
    data |= ((uint32_t)(schedules[i].active ? 1 : 0) << 24);
    
    preferences.putUInt(key, data);
  }
  
  preferences.end();
  Serial.printf("Saved %d schedules to flash\n", numSchedules);
}

void loadSchedules() {
  preferences.begin("schedules", true);
  
  numSchedules = preferences.getInt("count", 0);
  if (numSchedules > MAX_SCHEDULES) {
    numSchedules = MAX_SCHEDULES;
  }
  
  for (int i = 0; i < numSchedules; i++) {
    char key[16];
    sprintf(key, "sched%d", i);
    uint32_t data = preferences.getUInt(key, 0);
    
    schedules[i].id = data & 0x3F;
    schedules[i].hour = (data >> 6) & 0x1F;
    schedules[i].minute = (data >> 11) & 0x3F;
    schedules[i].daysOfWeek = (data >> 17) & 0x7F;
    schedules[i].active = ((data >> 24) & 0x01) != 0;
  }
  
  preferences.end();
  Serial.printf("Loaded %d schedules from flash\n", numSchedules);
}

bool checkSchedulesDue() {
  if (!timeIsSynchronized || numSchedules == 0) {
    return false;
  }
  
  int currentHour = timeinfo.tm_hour;
  int currentMinute = timeinfo.tm_min;
  int currentDayOfWeek = (timeinfo.tm_wday == 0) ? 0 : timeinfo.tm_wday - 1;
  int dayBit = 1 << currentDayOfWeek;
  
  for (int i = 0; i < numSchedules; i++) {
    if (!schedules[i].active) {
      continue;
    }
    
    if ((schedules[i].daysOfWeek & dayBit) == 0) {
      continue;
    }
    
    if (schedules[i].hour == currentHour && 
        schedules[i].minute == currentMinute) {
      return true;
    }
  }
  
  return false;
}

void alertScheduleDue() {
  for (int i = 0; i < 3; i++) {
    digitalWrite(compartment1_LED, HIGH);
    digitalWrite(compartment2_LED, HIGH);
    digitalWrite(compartment3_LED, HIGH);
    delay(300);
    digitalWrite(compartment1_LED, LOW);
    digitalWrite(compartment2_LED, LOW);
    digitalWrite(compartment3_LED, LOW);
    delay(300);
  }
}

void measureWeightAfterServo() {
  if (!weightMeasurementNeeded) return;
  
  if (millis() - servoCompletionTime >= servoSettlingTime) {
    float weight_mg = getFilteredWeight();
    Serial.printf("Post-dispense weight: %.2f mg\n", weight_mg);
    
    if (deviceConnected) {
      char buf[48];
      snprintf(buf, sizeof(buf), "POST_DISPENSE_WEIGHT: %.2f mg", weight_mg);
      pTxCharacteristic->setValue(buf);
      pTxCharacteristic->notify();
    }
    
    weightMeasurementNeeded = false;
  }
}

void calibrateScale(float knownWeightMg) {
  if (knownWeightMg <= 0) {
    Serial.println("Error: Calibration weight must be greater than 0");
    return;
  }
  
  Serial.println("Taring scale...");
  scale.tare(20);
  delay(1000);
  
  Serial.printf("Please place %0.2f mg reference weight on the scale\n", knownWeightMg);
  
  if (deviceConnected) {
    char buf[64];
    snprintf(buf, sizeof(buf), "PLACE_WEIGHT: %.2f mg", knownWeightMg);
    pTxCharacteristic->setValue(buf);
    pTxCharacteristic->notify();
  }
  
  delay(5000);
  
  calibrationReading = scale.read_average(30);
  
  if (calibrationReading != 0) {
    calibrationFactor = (float)calibrationReading / knownWeightMg;
    scale.set_scale(calibrationFactor);
    
    Serial.printf("Calibration complete! New factor: %f\n", calibrationFactor);
    calibrationWeight = knownWeightMg;
    
    if (deviceConnected) {
      char buf[64];
      snprintf(buf, sizeof(buf), "CALIBRATED: %.6f", calibrationFactor);
      pTxCharacteristic->setValue(buf);
      pTxCharacteristic->notify();
    }
  } else {
    Serial.println("Calibration failed: zero reading");
    if (deviceConnected) {
      pTxCharacteristic->setValue("CALIBRATION_FAILED: Zero reading");
      pTxCharacteristic->notify();
    }
  }
}

void startAutoCalibration(float knownWeightMilligrams) {
  if (knownWeightMilligrams <= 0) {
    Serial.println("Error: Calibration weight must be greater than 0");
    
    if (deviceConnected) {
      pTxCharacteristic->setValue("CALIBRATION_FAILED: Invalid weight");
      pTxCharacteristic->notify();
    }
    return;
  }
  
  knownWeightMg = knownWeightMilligrams;
  
  isAutoCalibrating = true;
  calibrationStep = 0;
  calibrationStartTime = millis();
  
  Serial.println("Starting automatic calibration sequence...");
  Serial.println("Step 1: Taring scale - remove all weight");
  
  if (deviceConnected) {
    pTxCharacteristic->setValue("AUTO_CAL_START: Remove all weight from scale");
    pTxCharacteristic->notify();
  }
}
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
void loop() {
  if (isScanning && !deviceConnected) {
    unsigned long currentMillis = millis();
    
    if (currentMillis - blinkInterval >= 500) {
      blinkInterval = currentMillis;
      bluetooth_LED_State = !bluetooth_LED_State;
      digitalWrite(bluetooth_LED, bluetooth_LED_State ? HIGH : LOW);
    }
  }
  
  if (isAutoCalibrating) {
    updateAutoCalibration();
  }
  
  if (weightMeasurementNeeded) {
    measureWeightAfterServo();
  }
  
  unsigned long currentMillis = millis();
  if (dispensePending && (currentMillis - lastDispenseCheck >= dispenseCheckInterval)) {
    lastDispenseCheck = currentMillis;
    
    if (currentMillis - lastServoActionTime >= servoCompletionTimeout) {
      digitalWrite(compartment1_LED, LOW);
      digitalWrite(compartment2_LED, LOW);
      digitalWrite(compartment3_LED, LOW);
      Serial.println("Dispense completed, LEDs turned off");
      dispensePending = false;
    }
  }
  
  if (currentMillis - lastTimeCheck >= timeCheckInterval) {
    lastTimeCheck = currentMillis;
    
    if (timeIsSynchronized) {
      timeinfo.tm_sec += 2;
      mktime(&timeinfo);
      
      if (deviceConnected) {
        pTxCharacteristic->setValue("CHECK_SCHEDULES");
        pTxCharacteristic->notify();
      } else {
        hasDueSchedules = checkSchedulesDue();
        
        if (hasDueSchedules) {
          Serial.println("Local schedule is due!");
          alertScheduleDue();
        }
      }
    }
  }
  
  if (deviceConnected && hasDueSchedules) {
    for (int i = 0; i < 2; i++) {
      digitalWrite(compartment1_LED, HIGH);
      digitalWrite(compartment2_LED, HIGH);
      digitalWrite(compartment3_LED, HIGH);
      delay(300);
      digitalWrite(compartment1_LED, LOW);
      digitalWrite(compartment2_LED, LOW);
      digitalWrite(compartment3_LED, LOW);
      delay(300);
    }
  }
  
  if (!weightMeasurementNeeded && millis() - lastWeightUpdate >= weightInterval) {
    lastWeightUpdate = millis();
    if (scale.wait_ready_timeout(500)) {
      float weight_mg = getFilteredWeight();
      Serial.printf("Weight: %.2f mg\n", weight_mg);
      if (deviceConnected) {
        char buf[32];
        snprintf(buf, sizeof(buf), "WEIGHT: %.2f mg", weight_mg);
        pTxCharacteristic->setValue(buf);
        pTxCharacteristic->notify();
      }
    } else {
      Serial.println("Load cell not ready.");
    }
  }
  
  delay(100);
}

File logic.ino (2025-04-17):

#include <Arduino.h>
#include <ESP32Servo.h>
#include "HX711.h"
#include <BLEDevice.h>
#include <BLEServer.h>
#include <BLEUtils.h>
#include <BLE2902.h>

// Nordic UART Service UUIDs
#define SERVICE_UUID        "6e400001-b5a3-f393-e0a9-e50e24dcca9e"
#define CHAR_UUID_RX        "6e400003-b5a3-f393-e0a9-e50e24dcca9e"  // for writing commands
#define CHAR_UUID_TX        "6e400002-b5a3-f393-e0a9-e50e24dcca9e"  // for notifications

// ----- Servo Setup -----
Servo servo1, servo2, servo3;
const int servo1Pin = 25;
const int servo2Pin = 22;
const int servo3Pin = 23;
// track current positions
int servo1Pos = 0;
int servo2Pos = 0;
int servo3Pos = 0;

// ----- LED Setup -----
const int ledPin = 12;
bool ledState = false;

// ----- HX711 Load Cell Setup -----
const int LOADCELL_DOUT_PIN = 32;
const int LOADCELL_SCK_PIN  = 33;
HX711 scale;

// ----- BLE Globals -----
BLECharacteristic *pTxCharacteristic;
bool deviceConnected = false;
unsigned long lastWeightUpdate = 0;
const unsigned long weightInterval = 5000;  // 5 s

// ----- BLE Server Callbacks -----
class MyServerCallbacks : public BLEServerCallbacks {
  void onConnect(BLEServer* pServer) override {
    deviceConnected = true;
    Serial.println("BLE Device Connected");
    // send help menu on connect
    const char* helpText =
      "CMDs:\n"
      "SERVO1 OPEN/CLOSE\n"
      "SERVO2 OPEN/CLOSE\n"
      "SERVO3 OPEN/CLOSE\n"
      "LED ON/OFF\n"
      "TARE\n"
      "RAW\n"
      "HELP";
    pTxCharacteristic->setValue(helpText);
    pTxCharacteristic->notify();
  }

  void onDisconnect(BLEServer* pServer) override {
    deviceConnected = false;
    Serial.println("BLE Device Disconnected");
    // Reset outputs on disconnect
    servo1.write(0); servo1Pos = 0;
    servo2.write(0); servo2Pos = 0;
    servo3.write(0); servo3Pos = 0;
    digitalWrite(ledPin, LOW); ledState = false;
    pServer->getAdvertising()->start();
    Serial.println("Advertising restarted");
  }
};

// ----- BLE Characteristic Callbacks -----
class MyCallbacks : public BLECharacteristicCallbacks {
  void onWrite(BLECharacteristic* pCharacteristic) override {
    String rx = pCharacteristic->getValue();
    if (rx.isEmpty()) return;

    String cmd = String(rx.c_str());
    cmd.trim();
    cmd.toUpperCase();
    Serial.print("Received command: ");
    Serial.println(cmd);

    // HELP
    if (cmd == "HELP") {
      const char* helpText =
        "CMDs:\n"
        "SERVO1 OPEN/CLOSE\n"
        "SERVO2 OPEN/CLOSE\n"
        "SERVO3 OPEN/CLOSE\n"
        "LED ON/OFF\n"
        "TARE\n"
        "RAW\n"
        "HELP";
      pTxCharacteristic->setValue(helpText);
      pTxCharacteristic->notify();
      return;
    }

    // TARE
    if (cmd == "TARE") {
      scale.tare();
      Serial.println("Scale tared.");
      pTxCharacteristic->setValue("OK: Scale tared");
      pTxCharacteristic->notify();
      return;
    }
    // RAW
    if (cmd == "RAW") {
      long raw = scale.read_average(5);
      char buf[32];
      snprintf(buf, sizeof(buf), "RAW: %ld", raw);
      Serial.println(buf);
      pTxCharacteristic->setValue(buf);
      pTxCharacteristic->notify();
      return;
    }

    // Servo 1
    if (cmd == "SERVO1 OPEN" && servo1Pos != 180) {
      servo1.write(175);
      servo1Pos = 180;
      Serial.println("Compartment 1 Opened");
    } else if (cmd == "SERVO1 CLOSE" && servo1Pos != 0) {
      servo1.write(10);
      servo1Pos = 0;
      Serial.println("Compartment 1 Closed");
    }

    // Servo 2
    if (cmd == "SERVO2 OPEN" && servo2Pos != 180) {
      servo2.write(168.5);
      servo2Pos = 180;
      Serial.println("Compartment 2 Opened");
    } else if (cmd == "SERVO2 CLOSE" && servo2Pos != 0) {
      servo2.write(10);
      servo2Pos = 0;
      Serial.println("Compartment 2 Closed");
    }

    // Servo 3
    if (cmd == "SERVO3 OPEN" && servo3Pos != 180) {
      servo3.write(175);
      servo3Pos = 180;
      Serial.println("Compartment 3 Opened");
    } else if (cmd == "SERVO3 CLOSE" && servo3Pos != 0) {
      servo3.write(10);
      servo3Pos = 0;
      Serial.println("Compartment 3 Closed");
    }

    // LED
    if (cmd == "LED ON" && !ledState) {
      digitalWrite(ledPin, HIGH);
      ledState = true;
      Serial.println("LED Turned ON");
    } else if (cmd == "LED OFF" && ledState) {
      digitalWrite(ledPin, LOW);
      ledState = false;
      Serial.println("LED Turned OFF");
    }
  }
};

void setup() {
  Serial.begin(115200);
  Serial.println("Starting Smart Pill Dispenser BLE App...");

  // LED
  pinMode(ledPin, OUTPUT);
  digitalWrite(ledPin, LOW);

  // Servos
  servo1.attach(servo1Pin);
  servo2.attach(servo2Pin);
  servo3.attach(servo3Pin);
  servo1.write(0);
  servo2.write(0);
  servo3.write(0);

  // Load cell init
  Serial.println("Initializing HX711...");
  scale.begin(LOADCELL_DOUT_PIN, LOADCELL_SCK_PIN);
  long initRead = scale.read();
  if (initRead <= 0) {
    Serial.println("WARNING: HX711 not detected!");
    // blink LED as warning
    for (int i = 0; i < 3; i++) {
      digitalWrite(ledPin, HIGH);
      delay(200);
      digitalWrite(ledPin, LOW);
      delay(200);
    }
  } else {
    Serial.println("HX711 connected.");
    scale.set_scale(420.0983);
    scale.tare();
  }

  // BLE init
  BLEDevice::init("SmartPillDispenser");
  BLEServer* pServer = BLEDevice::createServer();
  pServer->setCallbacks(new MyServerCallbacks());

  BLEService* pService = pServer->createService(SERVICE_UUID);

  // TX (notify)
  pTxCharacteristic = pService->createCharacteristic(
    CHAR_UUID_TX,
    BLECharacteristic::PROPERTY_NOTIFY
  );
  pTxCharacteristic->addDescriptor(new BLE2902());

  // RX (write)
  BLECharacteristic* pRxCharacteristic = pService->createCharacteristic(
    CHAR_UUID_RX,
    BLECharacteristic::PROPERTY_WRITE
  );
  pRxCharacteristic->setCallbacks(new MyCallbacks());

  pService->start();
  pServer->getAdvertising()->start();
  Serial.println("BLE Advertising Started");
}

void loop() {
  // Periodic weight notification
  if (millis() - lastWeightUpdate >= weightInterval) {
    lastWeightUpdate = millis();
    if (scale.wait_ready_timeout(500)) {
      float weight = scale.get_units(5);
      Serial.printf("Weight: %.2f g\n", weight);

      if (deviceConnected) {
        char buf[32];
        snprintf(buf, sizeof(buf), "WEIGHT: %.2f g", weight);
        pTxCharacteristic->setValue(buf);
        pTxCharacteristic->notify();
      }
    } else {
      Serial.println("Load cell not ready.");
    }
  }

  delay(100);
}

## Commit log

2025-03-01 Second Round Designs
    [Power Subsystem.kicad_pcb, Power Subsystem.kicad_sch]
2025-03-03 notebooks and pcbway
    [Third Design (PCBWay 1)-B_Cu.gbr, Third Design (PCBWay 1)-B_Mask.gbr, Third Design (PCBWay 1)-B_Paste.gbr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]
2025-03-04 3d models
    [Cavity Rotator-Body.stl, Rotating Chamber-Body.stl]
2025-03-12 New Schematic
    [Third Design (PCBWay 1)-B_Cu.gbr, Third Design (PCBWay 1)-B_Mask.gbr, Third Design (PCBWay 1)-B_Paste.gbr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]
2025-03-30 Notebook Entry
    [ECE 445 PCBWay Order 4-B_Cu.gbr, ECE 445 PCBWay Order 4-B_Mask.gbr, ECE 445 PCBWay Order 4-B_Paste.gbr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]
2025-05-03 3D Prints & Docs
    [Compartment 1.stl, Compartment 2.stl, Compartment 3.stl]
